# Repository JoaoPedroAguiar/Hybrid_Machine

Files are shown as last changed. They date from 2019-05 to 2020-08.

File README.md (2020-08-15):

# Hybrid_Machine
Development of a Hybrid Rapid Prototyping System Using 3D Printing Software and Arduino

Attention: This documentation is under construction.

Here, you can find all documents to replicate the project.
This machine was made to attain the title of electrical engineer, and with these documents is possible to make prototypes 
using hybrid manufacture, to save money no lost quality, and using fewer manufacturing materials. We have made it combining 
the best qualities of technology additive and subtractive.
I'm so sorry but the paper was written in the Portuguese language, probably I will write a new version in English still in 2020.

Thanks for reading and share your projects too.

Made in Brazil.

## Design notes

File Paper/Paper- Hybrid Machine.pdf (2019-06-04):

Resumo—Prototipagem rápida é um tecnologia imprescindível por possibilitar o desenvolvimento de novos produtos, e trazer uma economia de, pelos menos, 70% a 90% nos quesitos tempo e custo. Cada vez mais usadas, em consequência do barateamento das máquinas nos últimos anos. A manufatura híbrida surge com a tarefa de otimizar os processos de produção, combinando o que existe de melhor no método aditivo e subtrativo, para reduzir o volume de material, sem perder em acabamento e qualidade. A relevância da pesquisa está em apresentar uma máquina robusta e de fácil manuseio, que utiliza um sistema eletrônico de baixo custo e código fonte aberto. Que necessita de apenas um software de controle, para executar processos de manufatura híbrida, sendo uma opção aos métodos propostos anteriormente. Portanto, o objetivo da pesquisa é descrever os requisitos necessários para que se possa replicar o projeto, identificar melhorias, ilustrar os pontos fracos e apresentar os resultados. Construir um mancal, foi um sucesso, pois, permitiu demostrar de forma satisfatória, a eficiência do método. Capaz de construir peças complexas, com precisão e agilidade, em uma única estrutura mecânica.

Palavras Chave—manufatura aditiva, comando numérico computadorizado (CNC), manufatura híbrida, manufatura subtrativa, impressão 3D.

I. INTRODUÇÃO
prototipagem rápida é uma tecnologia que surgiu no final da década de 80. Com isso, foi possível construir peças a partir de um modelo tridimensional feito em programas CAD (Computer Aided Design – Desenho Assistido por Computador) [1]. Imprescindível por possibilitar o desenvolvimento de novos produtos em menor tempo e permitir verificar funcionalidades como forma, cor, tempo de manufatura e encaixes das peças [2]. Possibilitando, assim, uma maior interação com o projeto antes de ser produzido em escala, evitando retrabalhos e produtos lançados no mercado com falhas. E mais: a prototipagem pode trazer uma economia de, pelo menos, 70% a 90% nos quesitos tempo e custo [3] [4]. Duas variáveis importantíssimas para as indústrias que precisam manter a sua competividade no mercado e, ao mesmo tempo, necessitam entregar um produto de alta qualidade e acabamento impecável [5].
Com isso, sistemas híbridos de prototipagem rápida, que combinam tecnologias de deposição e remoção de material, estão sendo utilizados para otimizar a produção, integrando as características positivas de cada método [6]. A produção se torna mais eficiente quando se reduz o volume de material ao aplicar a manufatura aditiva. Esse método possui acabamento com pouca resolução. Logo, para contornar essa variável, utiliza-se, em conjunto, o processo de manufatura subtrativa, que é caracterizada por usinar as peças, remover rebarbas e eliminar deformações [7].
Para tanto, já existem máquinas híbridas contendo inúmeras ferramentas integradas a uma única estrutura mecânica, que combinam o processo de manufatura aditiva e subtrativa para criar peças otimizadas, como a de produção comercial Integrex i-400 AM [5]. Porém, a utilização desta técnica ainda é baixa, por se tratar de uma tecnologia recente e que tem sido embarcada em máquinas com alto custo de investimento. Logo, a comunidade científica tem publicado estudos visando democratizar a implementação do processo de manufatura híbrida. Para citar dois exemplos: a adaptação de ferramentas de fresagem em impressoras 3D [8], e até mesmo, a criação de uma máquina de 5 eixos, construída a partir do zero [9].
A relevância da pesquisa está em apresentar uma máquina robusta e de fácil manuseio, que utiliza um sistema eletrônico de baixo custo e código fonte aberto. Que necessita de apenas um software de controle [10] para executar processos de manufatura híbrida, como opção aos propostos anteriormente
[11] [9]. Portanto, o objetivo da pesquisa é descrever os requisitos necessários para que se possa replicar o projeto, identificar melhorias, ilustrar os pontos fracos e apresentar os resultados. Com a efetiva contribuição para a sociedade e meio ambiente, ao otimizar tempo e custo de produção, aproveitar melhor os recursos naturais e possibilitar uma gama maior de aplicações em apenas uma máquina. Sendo capaz de construir peças de alta complexidade, precisão e agilidade, mantendo os usuários competitivos frente aos desafios do mercado.
Por fim, vale ressaltar que esta é uma pesquisa open source, que visa apenas o compartilhamento de conhecimento com a comunidade científica, indexada publicamente na plataforma de hospedagem GitHub. Lá é possível encontrar toda documentação gerada durante a execução do trabalho como, vídeos, esquemáticos, firmware, modelos tridimensionais, fotos, parâmetros de configuração, manuais e artigos de referência [12].

# Desenvolvimento de um Sistema Híbrido de Prototipagem Rápida Utilizando Software de Impressão 3D e Arduino

Santos, P. A. Joao; Macedo, P. L. Pedro; Delmondes Rômulo; Araújo A. A. Marcelo

A

II. TÉCNICAS DE MANUFATURA
A manufatura é empregada em diversos campos, como medicina, educação, decoração, engenharia etc. Existem diversas técnicas e dentre as mais utilizadas podemos destacar duas delas: a aditiva, que consiste na impressão do objeto a partir do zero; e a subtrativa, cujo processo é realizado a partir da remoção do material. Contudo, estes dois métodos apresentam limitações e, se mal utilizados, podem gerar custos excedentes de produção. Nos últimos anos, a manufatura híbrida, método que combina a tecnologia aditiva e subtrativa, tem sido utilizada por reduzir custo e tempo de produção, se comparado com os métodos realizados separadamente [11].
A. Manufatura Aditiva
Esse processo é feito em camadas, que se sobrepõe uma a outra, como uma espécie de soldagem do material escolhido. Previamente, é realizado um desenho tridimensional em CAD do objeto. Para somente depois imprimir seu resultado. Hoje, a impressão 3D utiliza inúmeros materiais, como polímeros, pó, cerâmica, metal, compostos alimentícios, gel, concreto, dentre outros [13].
Logo, a tecnologia de manufatura aditiva é escolhida por usuários que visam construir peças de forma rápida e com alta complexidade, mas que não se preocupam tanto com o acabamento das mesmas [2]. Alguns exemplos bastantes conhecidos desse método: LENS (Laser Engineered Net Shaping – Modelagem por Laser de Engenharia), SLA (Stereolithography - Estereolitografia), SLS (Selective Laser Sintering – Sintetização por Laser Seletivo) e SDM (Shape Deposition Manufacturing) [14]. Apesar da manufatura aditiva apresentar detalhes de qualidade na impressão, sua popularidade aumenta a cada ano, tanto no meio acadêmico, como no comercial e pessoal. Acredita-se que o uso dessa tecnologia será bem frequente e comum, sendo possível confeccionar componentes elétricos e eletrônicos, como um smartphone [15].
B. Manufatura Subtrativa
A máquina de fresagem CNC é o melhor exemplo de máquina de manufatura subtrativa, cuja função principal é controlar os movimentos da ferramenta e peça de trabalho. Ela permite, sempre que necessário, a troca da fresa, broca e outras ferramentas [16]. Alguns métodos são mais utilizados para fazer a extração do material, dando, assim, a forma desejada, como fresamento, perfuração e torneamento.

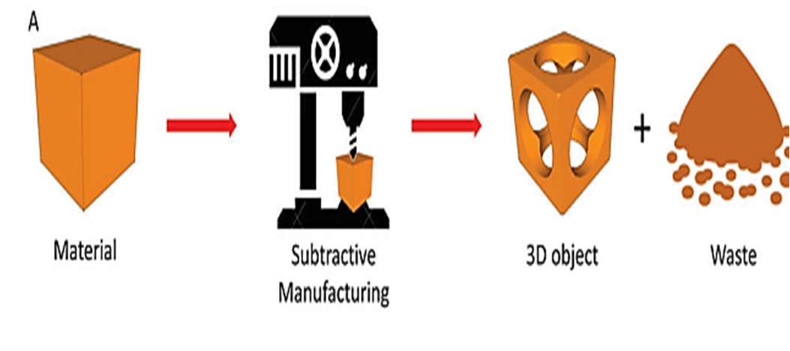
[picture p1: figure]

Fig. 1. Processos da tecnologia de manufatura subtrativa

Assim, sabe-se que a alta resistência das peças, ocorre devido sua única camada de matéria prima, fazendo com que o resto do desbaste não seja utilizado, Fig. 1 [17]. Algumas geometrias são incapazes de serem confeccionadas e a longa duração necessária para sua produção é uma das características negativas deste método [17].
C. Manufatura Híbrida
A manufatura híbrida une as melhores características de cada modelo citado, ao executar geometrias complexas, diminuir o tempo de produção e aproveitar melhor a matéria prima. Conforme a Fig. 2 [5], a primeira etapa consiste em adicionar material em camadas para construir um sólido de baixa resolução no menor intervalo de tempo e, em seguida, utilizar a tecnologia de manufatura subtrativa para cortar as rebarbas e melhorar o acabamento [9].
Características individuais presentes em cada processo podem ser encontradas em uma só máquina, que começa a surgir no mercado como a Integrex i-400 AM, modelo industrial que integra diversas tecnologias de manufatura [5].

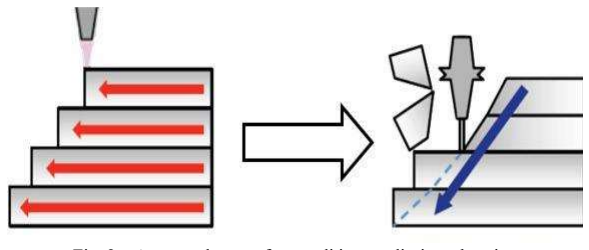
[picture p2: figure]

Fig. 2. A esquerda manufatura aditiva e a direito subtrativa.

III. FERRAMENTAS DE MANUFATURA
No mundo contemporâneo cria-se a necessidade de substituir as ferramentas pelas máquinas, a produção artesanal pela industrial e a energia humana pela energia eletromecânica. Dentro desse contexto, surge então a fresadora com comando numérico computadorizado (CNC). Marco relevante na história da indústria, por unir flexibilidade e versatilidade com precisão e um bom acabamento superficial. Diferente dos meios artesanais, que demandavam bastante tempo e não apresentavam a mesma qualidade [18].
Existem vários parâmetros que podem ser alterados no processo de manufatura. Alguns exemplos: determinação de ferramentas de trabalho, profundidade de corte, velocidade de avanço e velocidade de corte. As metodologias de remoção de material mais conhecidas são o torneamento, a fresagem, o aplainamento, a furação e a serragem [19].
Uma infinidade de materiais de manufatura pode existir quando se trata de produção aditiva e subtrativa. E podem ainda abranger diversas áreas, desde a confeitaria à corrida aeroespacial. Tratando-se de manufatura subtrativa, boa parte dos elementos conhecidos ou confeccionados pelo homem estão aptos para este método. Já na aditiva se destacam alguns, em específico, na forma de polímeros, como o PLA (Poly Lactic Acid - Poliácido Láctico) e o ABS (Acrylonitrile Butadiene Stryrene – Copolímero de Acrilonitrila) [2].

A. Ferramentas de Corte
A remoção do cavaco da peça é feita por usinagem, por meio de uma ferramenta de corte. A alta qualidade do processo está atrelada à eficiência desta ferramenta. Já o tempo de vida útil é diretamente proporcional ao tempo de corte efetivo das suas arestas de trabalho - antes de amolar ou fazer a troca da ferramenta [19].
O modelo mais comum de ferramenta de corte é a fresa. Bastante versátil, o instrumento é capaz de executar várias operações, como confeccionar roscas, abrir ranhuras e superfícies planas, e ainda fazer o processamento de engrenagens, dentre outras habilidades. Seus principais parâmetros: velocidade de corte, velocidade de avanço, penetração, taxa de remoção do material e tempo de produção. Existem quatro modelos diferentes de fresadoras; as verticais, as horizontais, as especiais e a universal. Elas podem ser utilizadas de duas maneiras – desde que sempre rotacione a ferramenta. Na fresagem cilíndrica, o eixo é paralelo à superfície; e na fresagem de topo (ou frontal), está perpendicular à área de trabalho. Conforme a Fig. 3 [18].

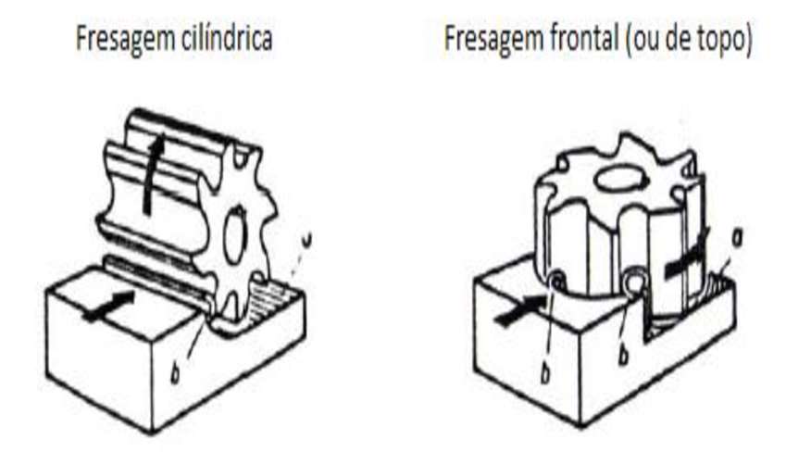
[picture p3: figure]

Fig. 3. Métodos de fresagem

B. Materiais de Impressão
Diversos materiais podem ser utilizados para a confecção de objetos 3D, incluindo metais, cerâmicas, polímeros, compostos alimentícios e sistemas biológicos [13]. São, basicamente, três estágios de manipulação: líquido, pó ou sólido base [7]. Em tese, os polímeros são os mais utilizados atualmente para impressão. Exemplos: PLA, ABS, policarbonatos, nylon e PETG (Polyethylene Terephthalate Glycol – Polietileno Tereftalato Glicol). Existem também materiais que, caso exposto a raios gama ou à óxido de etileno, se solidificam, comumente usados em tecnologias médicas [16].
O PLA é o filamento mais utilizado por não ser tóxico, ser biodegradável e possuir baixa temperatura para ponto de fusão, tornando-o mais ecologicamente sustentável [20]. Mesmo apresentando características mecânicas superiores e custo reduzido, o ABS não é tão usual quanto os demais. Isso devido à liberação de gases tóxicos e à maior exigência de temperatura de trabalho da extrusora, assim como da mesa aquecida. O PETG é considerado como o meio termo entre ABS e PLA, sendo mais durável e flexível que o PLA, e ainda mais fácil de imprimir que o ABS [21].

IV. MATERIAIS E MÉTODOS
Pesquisa exploratória e experimental, iniciada como tema de Trabalho de Conclusão de Curso, em 2016 [22], com foco na construção de uma máquina capaz de confeccionar placas de circuito impresso, de estrutura robusta e intercambiável. Conforme Fig. 4 [22]. Em 2017, novos objetivos foram traçados, a fim de tornar a movimentação da máquina intercambiável entre impressora 3D e fresadora CNC. Nessa, nova fase, damos continuidade ao trabalho, para que sejam feitas modificações na estrutura mecânica, elétrica e eletrônica. Objetivo: torná-la híbrida, de fácil manuseio e com troca rápida de ferramentas de fixação. Para isso, mantemos a proposta inicial de ser uma máquina modular, robusta e de fácil manuseio.

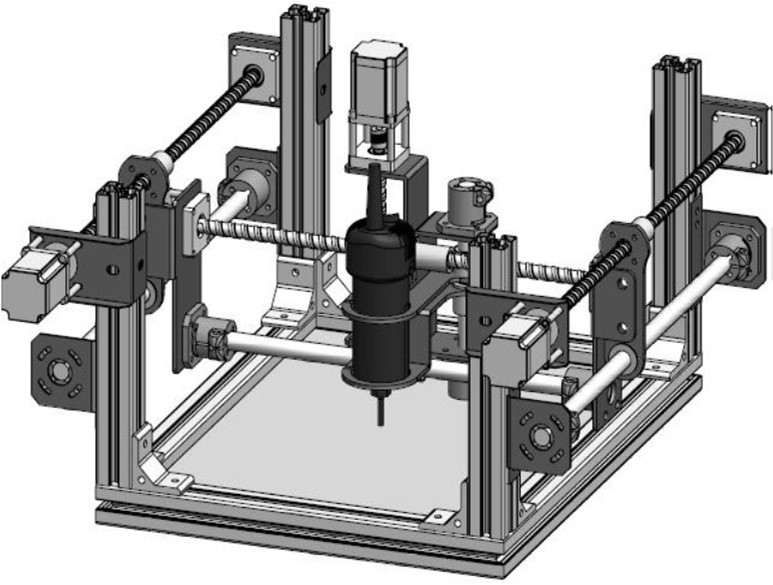
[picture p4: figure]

Fig. 4. Máquina intercámbiavel

A eletrônica da máquina é composta pelo sistema embarcado Arduino Mega, conectada ao módulo complementar de acionamento, Ramps 1.4. O Arduino é carregado com o firmware Marlin, que possui rotinas e estruturas lógicas adequadas ao projeto, todos de código fonte aberto, com atualizações constantes. Máquinas industriais empregam apenas um software de controle com funções nativas, para executar processos de manufatura híbrida. Porém, esses programas possuem rotinas de criptografia que bloqueiam a utilização em máquinas que não sejam produzidas por esses fabricantes. Até o presente momento, a pesquisa não identificou um software aberto aos usuários, com funções nativas de manufatura híbrida. Entretanto, alguns estudos têm apresentado alternativas que possibilitam a utilização desta técnica.
A primeira delas [11] consiste em utilizar dois softwares de controle distintos, para executar a manufatura aditiva e subtrativa, em ambientes de controle e supervisão separados. Pois, são encontrados inúmeros softwares abertos e dedicados à tecnologia, com suporte para serem empregados em conjunto com o sistema embarcado Arduino Mega. Em outro estudo [7], utiliza-se um software aberto e comercial, em conjunto com um programa desenvolvido pelos pesquisadores, que permite movimentar as ferramentas em uma máquina de cinco eixos. Como alternativa, apresentamos uma metodologia que utiliza apenas o software aberto de impressão, Simplifly3D, que depende apenas de algumas modificações não usuais, para construir uma peça efetivamente híbrida [12].

V. RESULTADOS
A primeira tarefa foi reinstalar [22] a tupia elétrica de 530 watts - com velocidade regulada de 0 a 30 mil rotações por minuto - à estrutura mecânica. Conforme a Fig. 5. Ela é responsável por rotacionar uma fresa instalada em seu eixo, tornando possível fresar na vertical sólidos de diversos materiais, como alumínio, madeira e plástico.

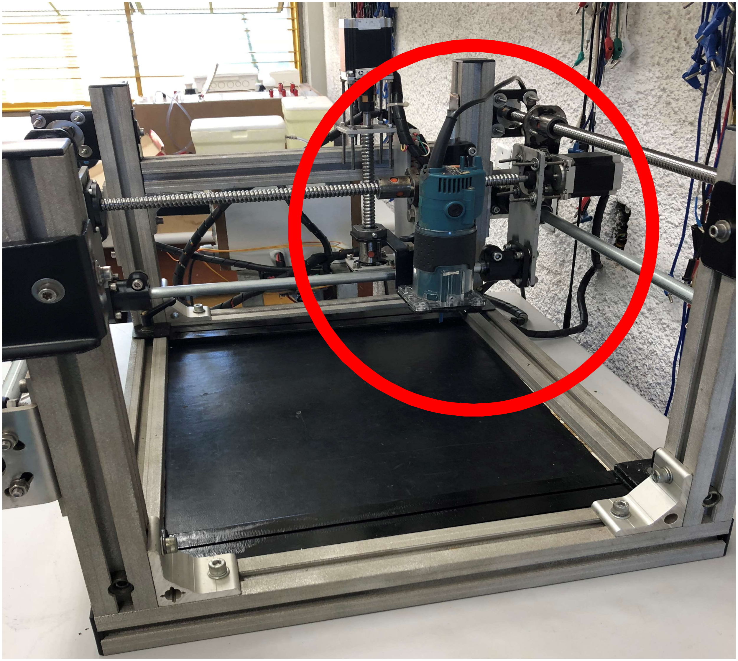
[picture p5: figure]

Fig. 5. Tupia fixada na máquina

A regulagem de altura é feita de forma manual, rápida e sem a utilização de ferramentas. Assim, após a instalação da tupia, que possuiu cerca de 1500 gramas, testes foram realizados para corrigir os parâmetros de movimentação decorrente do peso acrescentado à estrutura mecânica. A Tabela 1 apresenta as novas velocidades de trabalho da máquina, reconfiguradas no firmware Marlin.

TABELA I. DADOS DE VELOCIDADE

Parâmetros Configurados no Software Simplify3D
Retraction Speed (mm/min) | Default Printing Speed (mm/min) | X/Y Axis Movement Speed (mm/min) | Z Axis Movement Speed (mm/min) | X/Y Probe Speed (mm/min)
402.0 | 600.0 | 600.0 | 600.0 | 300.0

Para validar a utilização da máquina em processos de manufatura subtrativa foi elaborado um modelo tridimensional no software de modelagem Blender. Esse modelo possuiu espessura uniforme de 3 mm, carregado no Simplify3D, conforme a Fig. 6, para ser manufaturado em três materiais: MDF (Medium-Density Fiberboard), acrílico e placa de fenolite. Como as peças que seriam fresadas tem no máximo 3mm de profundidade, é imprescindível o uso da função de auto nivelamento. Ela compensa em software os desníveis da superfície, mapeando diversos pontos dá área de trabalho [23] [10]. Com o término do processo, os dados são gravados na memória não volátil do microcontrolador Atmega 2560, presente no Arduino Mega. Isso possibilita a leitura dos dados mesmo após desenergizar o sistema. Dessa forma, o processo é executado apenas quando a estrutura é movimentada.

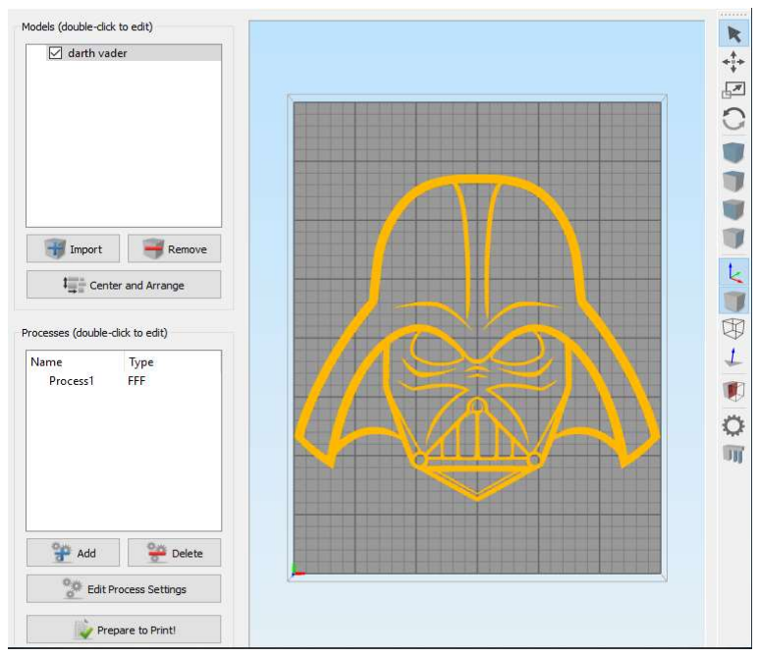
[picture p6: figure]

Fig. 6. Modelo tridimensional

Após o nivelamento, algumas funções foram habilitadas e configuradas, para permitir que o software execute processos de manufatura subtrativa, tendo em vista que ele não possuiu funções e suporte nativo para este tipo de aplicação, conforme os parâmetros presentes no folder (Router CNC Configuration), hospedado no GitHub [12]. Possibilitando, assim, o início dos testes de validação da tecnologia de manufatura subtrativa, o primeiro material utilizado foi o MDF, por apresentar características mecânicas favoráveis de fresagem. Na Fig. 7 é apresentado o resultado do processo que utilizou uma fresa reta de 6mm de diâmetro acoplada à tupia e metade da velocidade nominal, o modelo foi fatiado em três camadas de 1mm, para que a ferramenta penetrasse o MDF gradualmente.

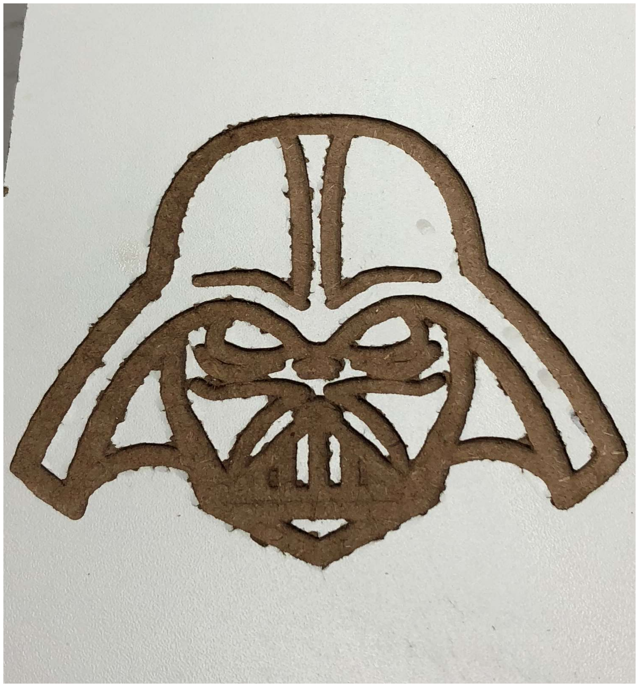
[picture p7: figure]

Fig. 7. Manufatura subtrativa em MDF

Outros dois materiais foram selecionados para serem fresados conforme a Fig. 8, o acrílico na parte superior, com configurações idênticas ao utilizado no MDF, e na parte inferior da Fig. 8, uma placa de fenolite com penetração unitária de 1 mm, fresa reta de 3.2 mm de diâmetro e velocidade nominal da tupia. Ao término, foi iniciado a implementação da tecnologia de manufatura aditiva à máquina. Para tal, foi necessário introduzir novos componentes elétricos e eletrônicos ao sistema, como mesa aquecida, extrusora, sensores de temperatura, relé de estado sólido e troca dos conectores do módulo Ramps por um modelo que possui proteção contra inversão de polaridade e maior resistência mecânica.

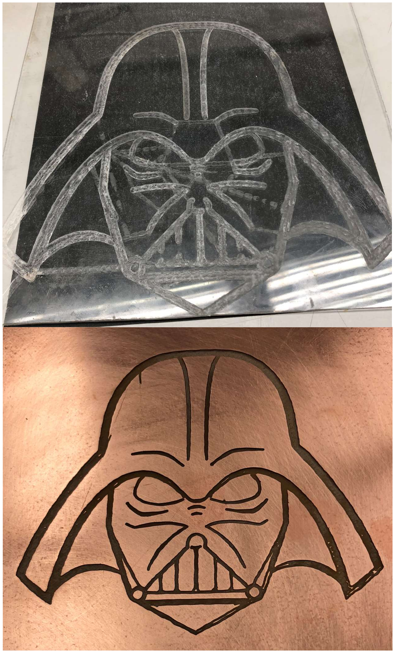
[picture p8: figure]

Fig. 8. Manufatura subtrativa em acrílico e placa de fenolite

Portanto, visto que a extrusora não possuiu o mesmo formato que a tupia, um suporte mecânico foi construído para que ela possa ser inserida no mesmo local. Conforme a Fig. 9. Esse suporte possui dois componentes móveis, para ajustar a posição do bico da extrusora em relação à superfície de impressão. Para executar uma troca rápida entre tupia e extrusora, foram utilizados quatro ímãs de neodímio com 10 mm de diâmetro por

### 4 mm de espessura, que atraem o suporte da extrusora à

estrutura mecânica do eixo Z, excluindo o uso de ferramentas para fixação. Conforme a Fig. 9. A troca é feita aplicando um esforço com as mãos no sentido contrário ao campo magnético do ímã.

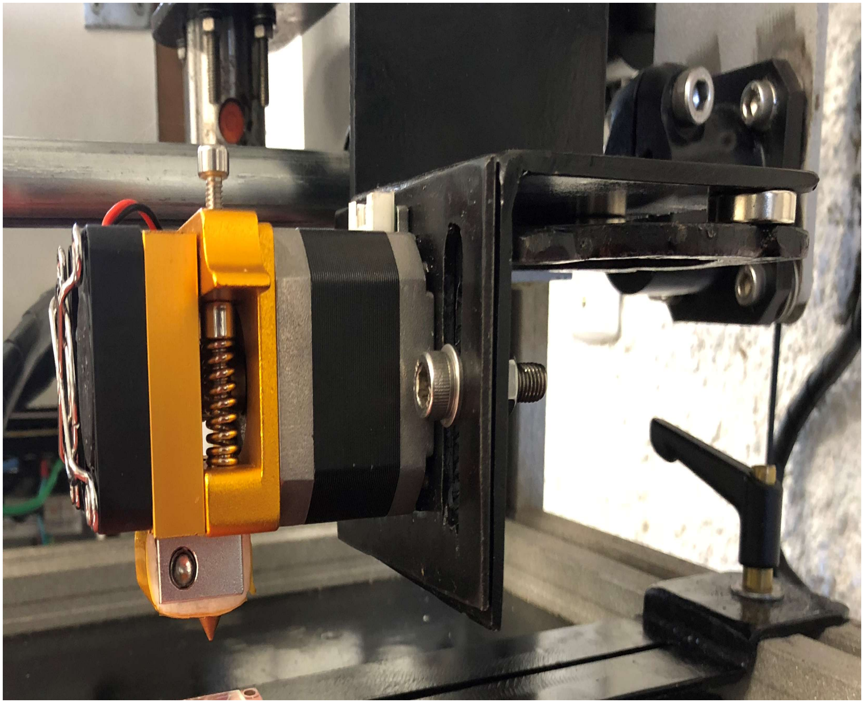
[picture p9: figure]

Fig. 9. Suporte de fixação da extrusora com ímãs de neodímio

Em seguida, duas guias metálicas ajustáveis foram inseridas para fixar a mesa aquecida. De acordo com a Fig. 10. A principal função das guias é descartar a necessidade de furar qualquer ponto da estrutura, caso seja necessário modificar a posição da mesa. Para iniciar o processo de impressão, foi selecionado o material ABS, que precisa ser aquecido pela extrusora, em temperaturas que vão de 230ºC à 240ºC.

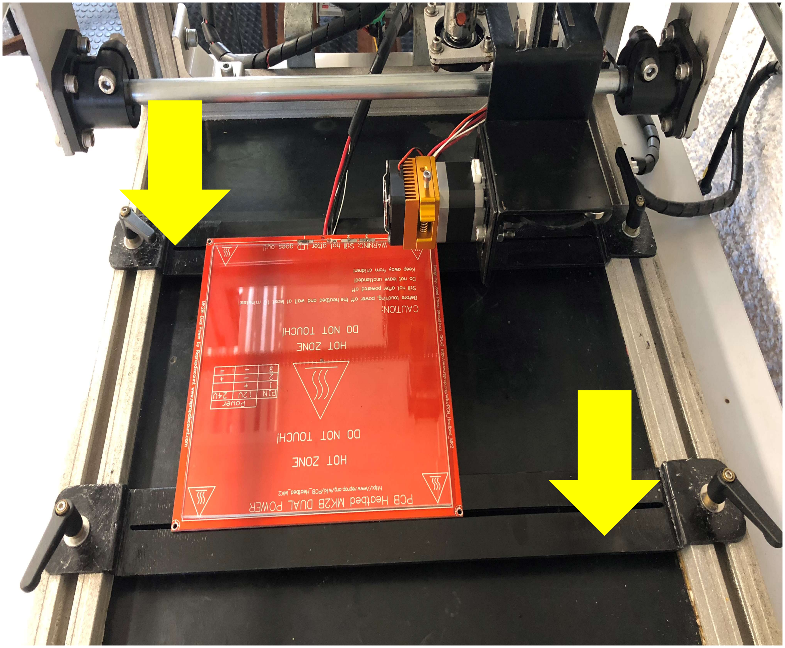
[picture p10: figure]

Fig. 10. Suporte da mesa aquecida

Entretanto, foi necessário controlar a temperatura da extrusora por um controlador proporcional integral derivativo (PID), obtendo maior estabilidade e precisão do sistema. Conforme o controle de malha fechada apresentada na Fig. 11. Desta maneira, a temperatura da extrusora é controlada, variando a tensão média sobre os terminais da resistência de aquecimento por PWM (Pulse Width Modulation – Modulação por Largura de Pulso). Pois a temperatura da resistência varia em função da tensão aplicada.

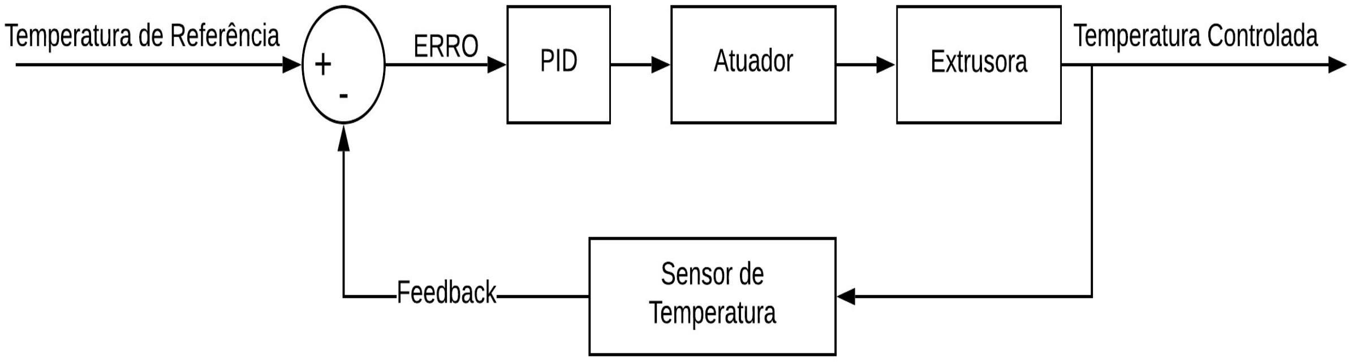
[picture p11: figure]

Fig. 11. Controle de Macha Fechada

Para facilitar a implementação do PID, o firmware Marlin apresenta uma rotina no código chamada de PID Autotune, que utilizada o método de ajuste Ziegler-Nichols [24]. Esse é um método heurístico que define os termos dos controladores proporcional, integral e derivativo - automaticamente. Apresentamos, na Tabela 2, os valores medidos experimentalmente, que definem o desempenho do controlador, em função da quantidade de ciclos de otimização.

TABELA II. DESEMPENHO DO CONTROLADOR PID

Parâmetros Medidos em Laboratório
Ciclos | 8 | 10 | 20
Controlador Proporcional (KP) | 16,87 | 15,75 | 15,95
Controlador Integral (KI) | 1,2 | 1,06 | 1,09
Controlador Derivativo (KD) | 59,43 | 58,51 | 58,14
Set Point (°c) | 230 | 230 | 230
Temperatura Inicial (°c) | 25 | 26 | 26,5
Tempo de Assentamento (s) | 101 | 132 | 139
Tempo de Pico (s) | 101 | 115 | 104
Ultrapassagem Percentual (%) | 0,87 | 0,3 | 0,41
Erro Permanente (°c) | 4 | 1,56 | 1,81

Para imprimir com ABS, a mesa também precisa ser aquecida com uma temperatura de aproximadamente 100°C, para auxiliar a aderência do filamento sobre a superfície.

Porém, não foi necessário realizar o controle PID, pois a temperatura máxima alcançada ficou próximo de 100°C. Assim, a mesa só é acionada antes de iniciar a impressão. E desligada após o término, pelo relé de estado sólido. Concluindo, neste momento, todas as modificações pertinentes. Resultado que pode ser visto no diagrama de blocos da Fig. 12.

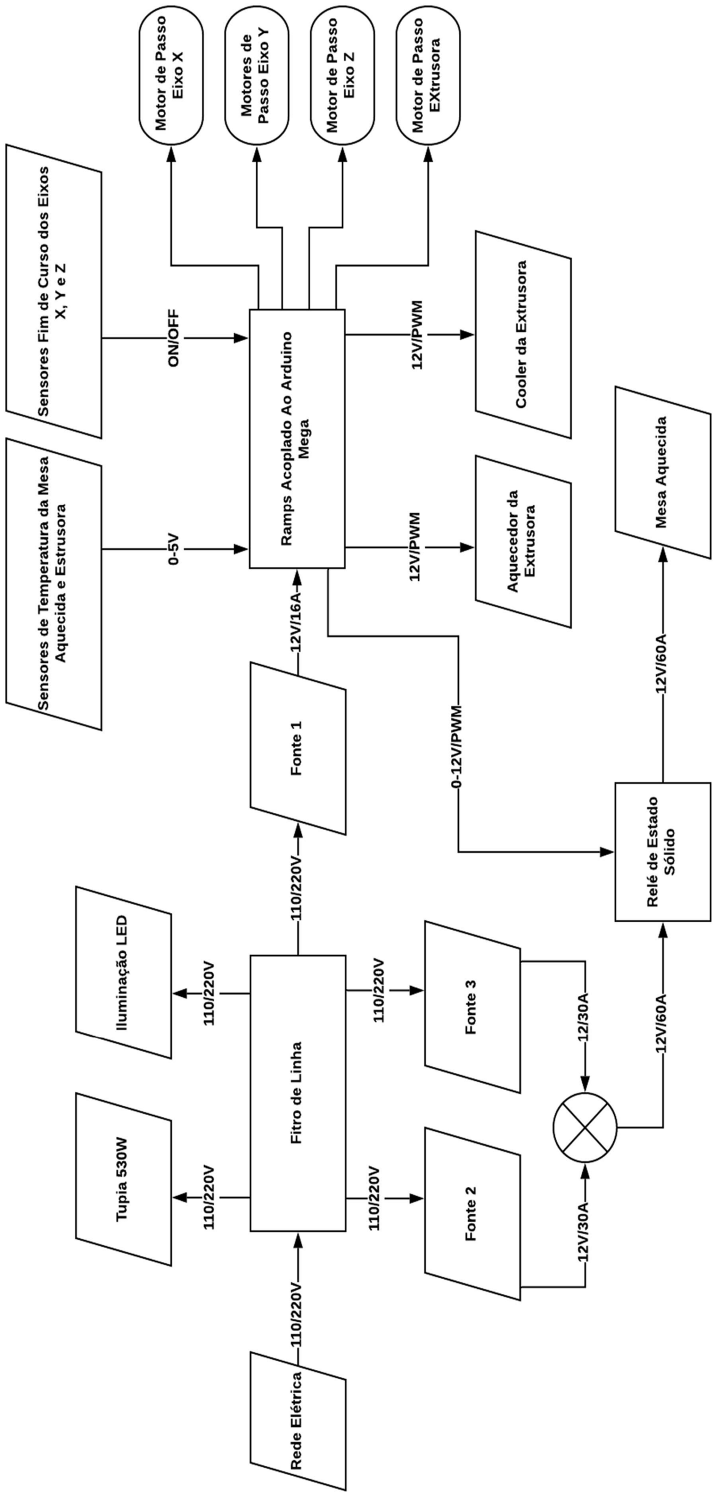
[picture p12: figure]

Fig. 12. Diagrama de Blocos da Máquina

Para encontrar os parâmetros de funcionamento da função de impressão 3D, algumas peças foram impressas em pequena escala para avaliar quais valores poderiam ser otimizados. Conforme Tabela 3. Pois, como o modelo mecânico da máquina é único, não foi possível usar dados de outra máquina como referência. Vale ressaltar, ainda, que todas as peças impressas foram feitas utilizando ABS de 1.75mm e bico extrusor de 0.6mm de diâmetro.

TABELA 3. CONFIGURAÇÃO UTILIZADA NO PROCESSO DE IMPRESSÃO

Parâmetros Configurados no Software Simplify3D
Retraction Speed (mm/min) | Default Printing Speed (mm/min) | X/Y Axis Movement Speed (mm/min) | Z Axis Movement Speed (mm/min) | Infill Percentage (%)
350 | 450 | 450 | 250 | 50

O sólido selecionado para ser impresso foi um mancal. Por fazer parte dos requisitos necessários para melhorar a estabilidade da máquina. Está peça demorou aproximadamente onze horas e doze minutos para ser impressa e gastou 48 gramas de filamento - em um total de 15,6 metros. Conforme Fig. 13. Logo após, a extrusora é substituída pela tupia, para que a peça seja fresada e acabada, até chegar ao estado final projetado. Esse modelo foi concebido para ser confeccionado utilizando a tecnologia de manufatura híbrida.

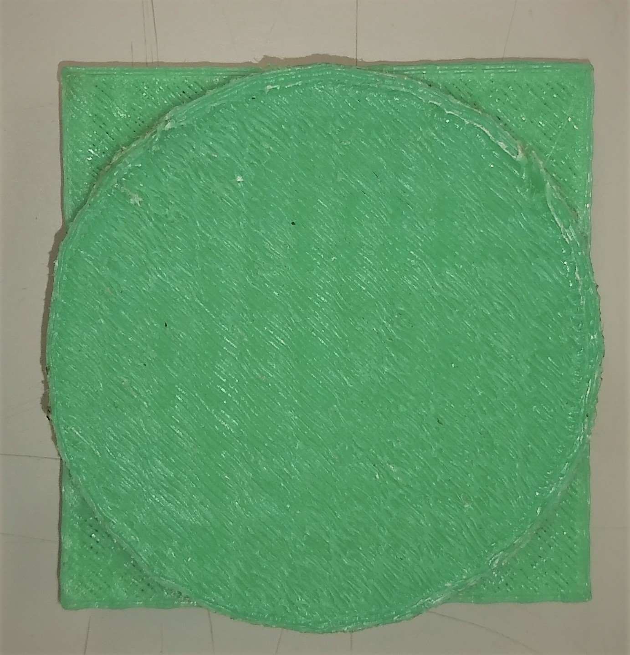
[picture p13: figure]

Fig. 13. Mancal Impresso

Com isso, uma ferramenta de corte de 3.2 mm de diâmetro é fixada junto à tupia, para fresar quatro furos nas extremidades. Conforme Fig. 14. O processo levou cerca de dois minutos para ser concluído, utilizando os parâmetros de velocidade apresentados na Tabela 1. Esses furos, vale frisar, não foram feitos inicialmente, porque a técnica subtrativa apresenta características mais favoráveis, como precisão e acabamento

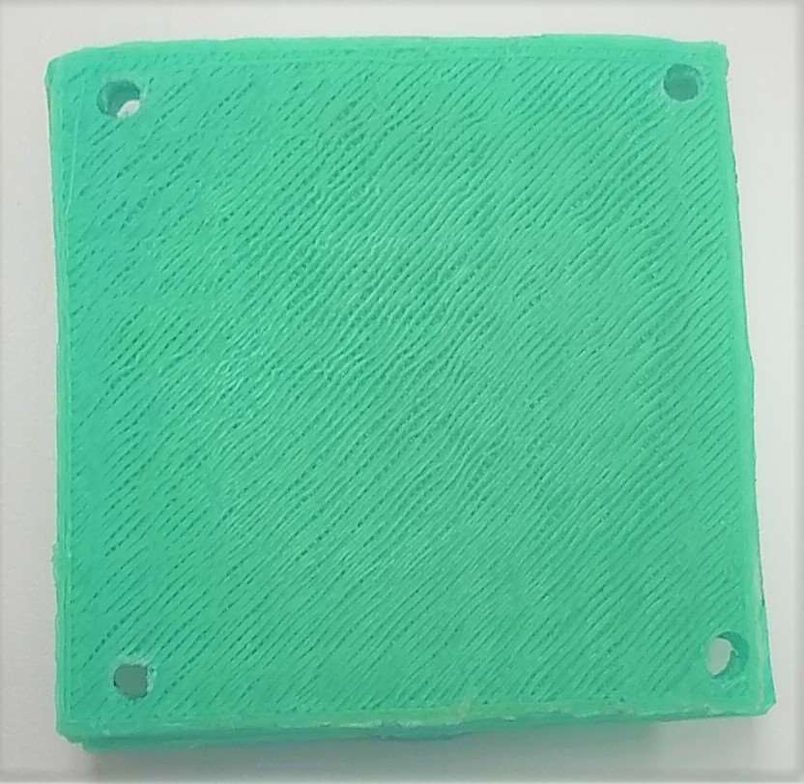
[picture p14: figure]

Fig. 14. Primeira Parte do Fresamento

Por fim, é dado continuidade ao processo, fresando a parte interna da peça, com a tupia em velocidade nominal – evitando assim o travamento do eixo de rotação. Esse processo demorou apenas seis minutos para ser finalizado, apresentando um bom acabamento interno. Conforme Fig. 15. Portando, esta peça apresenta o resultado, do sistema híbrido de prototipagem rápida utilizando software de impressão 3D e Arduino.

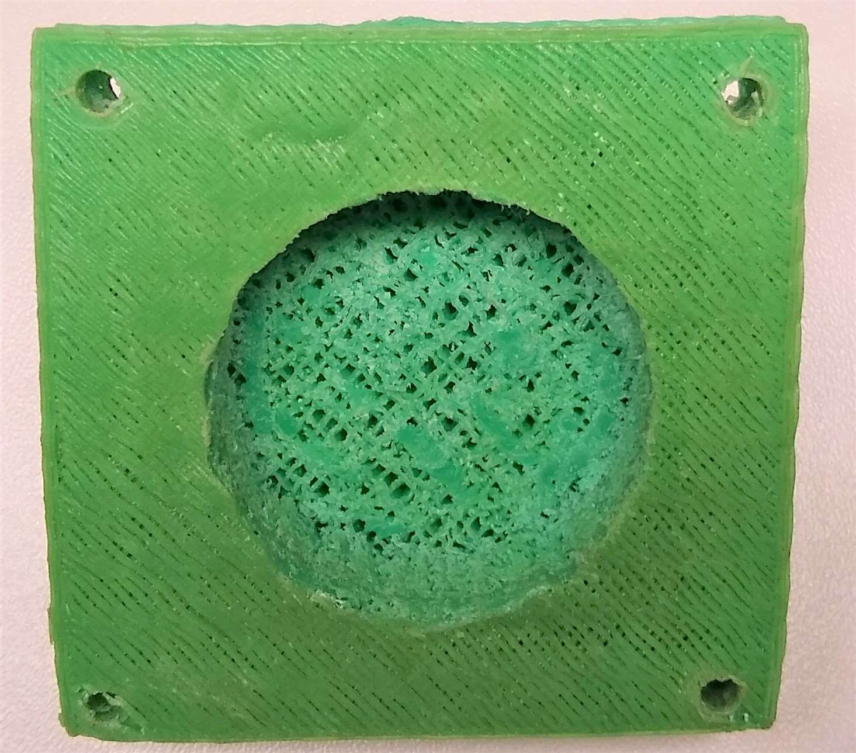
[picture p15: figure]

Fig. 15. Acabamento Final

O resultado da máquina, com todos os periféricos devidamente instalados e configurados, pode ser visto na Fig.

### 16. Um acervo com a documentação completa da máquina, está

indexado publicamente na plataforma online GitHub [12].

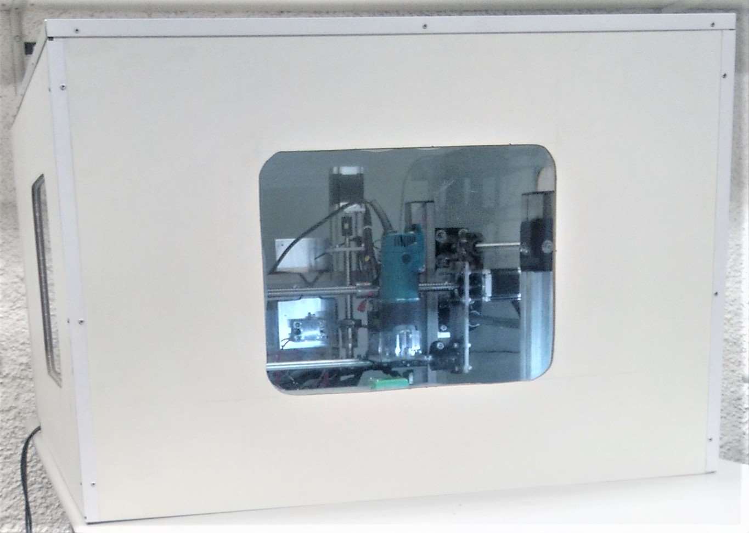
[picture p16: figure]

Fig. 16. Máquina Híbrida Utilizada

VI. DISCUSSÕES
A instalação da tupia à estrutura resultou no aumento do esforço realizado pelos motores para movimentar a mesa. Contudo, a intensidade de corrente fornecida foi elevada para aumentar a faixa de torque, juntamente com a diminuição da velocidade dos eixos. Isso permitiu que a máquina conseguisse, além de movimentar o peso excedente, realizasse esforços ao fresar materiais mais duros como o acrílico. Porém, o acionamento e o controle de velocidade da tupia ainda são feitos de forma manual. Assim, caso o processo de manufatura termine, o usuário precisa desligar a tupia manualmente.
Vale ressaltar: para tornar o processo mais eficiente é necessário utilizar de forma consciente as ferramentas de trabalho, selecionando sempre a mais adequada para cada material [24]. As fresas utilizadas foram todas selecionadas de acordo com o material fresado, evitando esforços excedentes pela máquina realizar o corte. Testes utilizando materiais mais duros, como ligas metálicas, por exemplo, podem requisitar mais torque dos motores. Contudo, os ensaios desses materiais não foram executados porque a extrusora não é capaz de utilizar materiais metálicos.
O software Simplify3D foi capaz de suportar a utilização da tupia mesmo sem suporte para este tipo de ferramenta. Entretanto, o fatiamento do modelo tridimensional - que define como a ferramenta irá se movimentar - é dedicado aos processos de manufatura aditiva. Com isso, o caminho pelo qual a fresa irá percorrer pode não ser o mais otimizado para este tipo de aplicação. A utilização do suporte com ímãs nas extremidades permitiu que a troca de ferramentas seja feita de forma rápida e descomplicada. O método, comparado com máquinas industriais que possuem sistemas automatizados de troca, possibilitou a redução de custo de fabricação e a maior facilidade de implementação.
Quanto à impressão 3D, inicialmente, a mesa aquecida não estava alimentada pela tensão da fonte de 12 volts, sendo apenas ligada e desligada pelo relé de estado sólido. A ideia era aplicar a tensão da rede de 220V sobre a mesa, variando o valor médio da tensão por PWM, utilizando o controlador PID. A principal vantagem estaria em alcançar os valores de setpoint, de forma mais rápida. Porém, a resistência de 0,3 Ohm é muito baixa para este tipo de aplicação. Pois, caso o sistema embarcado trave, a mesa pode exigir uma corrente de aproximadamente 733 amperes, causando o acionamento do sistema de proteção contra curto circuito da instalação elétrica.
Já na parte de extrusão, as peças começaram a empenar as bordas curvando se para cima, descolando as primeiras camadas, esse problema impossibilitava o término do processo. Pois, devido ao aumento de altura da peça, o bico da extrusora acabava empurrando a peça para outra posição, inutilizando o protótipo. Em um dos casos o problema foi tão sério, que o vidro que fica em cima da mesa aquecida acabou quebrando, junto aos acoplamentos dos motores. Pois, a peça conseguiu bloquear um dos eixos da máquina. Para contornar este problema, um gabinete foi construído. Conforme Fig. 16. Com o intuito de manter a temperatura interna constante, pois o ABS é um termoplástico que sofre contração, caso a peça seja exposta à variação de temperatura.
Outro ponto que merece bastante atenção, está relacionado com os problemas de EMC (Electromagnetic Compatibility – Compatibilidade Eletromagnética) que impedem que a máquina complete qualquer trabalho de impressão. O primeiro, causado por EMI (Eletromagnetic Interference – Interferência Eletromagnética), reiniciava o microcontrolador, devido à proximidade do Arduino Mega, em relação aos cabos pelo qual fluía toda corrente alternada, drenada pelas fontes chaveadas. O problema foi resolvido apenas aumentando a distância do cabo, em relação ao Arduino. No segundo caso, o microcontrolador travava, sem que qualquer mensagem de erro fosse retornada, voltando ao normal só após resetar o microcontrolador. Resolvido, trocando o cabo de comunicação - do Arduino com o computador - por um modelo com blindagem eletrostática e filtro de supressão de ruídos de alta frequência, conhecido como Ferrite Bead.

VII. CONSIDERAÇÕES FINAIS
A utilização do conjunto de baixo custo e open source, Arduino Mega, módulo Ramps 1.4 e firmware Marlin, combinados com o software aberto de controle e supervisão, Simplifly3D. Foi um sucesso por permitir que processos de manufatura híbrida, fossem realizados facilmente a partir de um único software. Embarcados em uma estrutura mecânica robusta e de fácil manuseio, viabilizado pela utilização de ímãs e conectores de engate rápido com proteção contra inversão de polaridade, tornando a troca de periféricos mais rápida e segura. Fresar a placa de fenolite, permitiu identificar que ainda é possível produzir placas de circuito impresso. Conforme visto na parte inferior da Fig. 8. Apenas modificando alguns parâmetros de movimentação, preservando a concepção inicial da máquina [22]. A construção do mancal permitiu demonstrar de forma satisfatória a proposta do estudo. Porém, acreditasse que o processo poderia ter sido otimizado imprimindo a peça com os cinco furos, com o diâmetro um pouco menor do que o esperado. Logo, a ferramenta cortaria menos material, sendo usada apenas para dar acabamento, reduzindo a quantidade de matéria prima, e o tempo necessário para imprimir e fresar. Recomenda-se, que os trabalhos futuros se concentrem em: desenvolver um sistema embarcado que seja imune aos problemas de EMI encontrados, repensar o layout da estrutura mecânica, desenvolver um software com funções nativas, imprimir com metal, criar laços com empresas e institutos de pesquisa que tenham interesse em investir no projeto. Como também, produzir protótipos encomendados pela comunidade, com o intuito de financiar bolsas de pesquisa, melhorias e aquisição de equipamentos para o laboratório. E, utilizá-la como ferramenta de popularização da ciência e tecnologia, preservando as características open source do projeto.

REFERÊNCIAS
[1] J. Fogiatto, "O uso da prototipagem rápida na área médico-odontológica", Revista Tecnologia & Humanismo, no. 30, pp. 60-68, 2006.
[2] J. Nagel, "Hybrid Manufacturing System Design and Development", in 38th Design Automation Conference, Chicago, 2012, pp. 189-198.
[3] C. Ahrens and N. Volpato, Prototipagem rápida, 1st ed. São Paulo: Edgard Blücher, 2007.
[4] A. Gorni, "Introdução à prototipagem rápida e seus processos."Plástico Industrial, pp. 230-239, 2001.
[5] T. Yamazaki, "Development of A Hybrid Multi-tasking Machine Tool: Integration of Additive Manufacturing Technology with CNC Machining", in 18th CIRP Conference on Electro Physical and Chemical Machining (ISEM XVIII), Oguchi, 2016, pp. 81-86.
[6] Z. Zhu, V. Dhokia and S. T. Newman, "A novel process planning approach for hybrid manufacturing consisting of additive, subtractive and inspection processes,"2012 IEEE International Conference on Industrial Engineering and Engineering Management, Hong Kong, 2012, pp. 1617-1621.
[7] W. Lee, C. Wei and S. CHUNG, "Development of a hybrid rapid prototyping system using low-cost fused deposition modeling and five-axis machining.", Journal of Materials Processing Technology, vol. 241, no. 11, pp. 2366-2374, 2014.
[8] G. Anzalone, B. Wijnen and J. Pearce, "Multi-material additive and subtractive prosumer digital fabrication with a free and open-source convertible delta RepRap 3-D printer", Rapid Prototyping Journal, vol. 21, no. 5, pp. 506-519, 2015.
[9] A. Kale, A. Kumar, M. Kumar and M. Prakasah, "Optimization of hybrid manufacturing process parameters by using FDM in CNC machine", in IOP Conference Series: Materials Science and Engineering, Kattankulathur, 2018, p. 012088.
[10] J. Santos, "Investigação e Aperfeiçoamento de um Sistema de Impressão 3D e Fresagem Intercambiável", 4th Brazilian Technology Symposium, 2018.
[11] P. Jorge Rodriguez, I. Pavel and A. Choudhury, "Development of a 3-D Printer and CNC Milling Desktop Machine for Manufacturing Labs", in ASEE Annual Conference & Exposition, New Orleans, 2016.
[12] J. Santos and P. Macedo, "JoaoPedroAguiar/Hybrid_Machine", GitHub,
2019. | [Online]. | Available:
https://github.com/JoaoPedroAguiar/Hybrid_Machine. [Accessed: 25-May- 2019].
[13] W. Frazier, "Metal Additive Manufacturing: A Review", Journal of Materials Engineering and Performance, pp. 1917-1928, 2014.
[14] K. Karunakaran, S. Suryakumar, V. Pushpa and S. Akula, "Low cost integration of additive and subtractive processes for hybrid layered manufacturing", Robotics and Computer-Integrated Manufacturing, no. 5, pp. 490-499, 2010.
[15] D. Espalin, D. Muse, E. MacDonald and R. Wicker, "3D Printing multifunctionality: structures with electronics", The International Journal of Advanced Manufacturing Technology, pp. 963-978, 2014.
[16] M. Müller and E. Wings, "An Architecture for Hybrid Manufacturing Combining 3D Printing and CNC Machining", International Journal of Manufacturing Engineering, vol. 2016, pp. 1-12, 2016.
[17] K. Boivie, S. Dolinsek and D. Homar, "Hybrid manufacturing; integration of additive technologies for competitive production of complex tools and products", in 15th International Research/Expert Conference, Prague, 2011.
[18] D. Pereira, "Estudo comparativo da vida útil das ferramentas e acabamento superficial para diferentes ferramentas de fresagem", Master, Escola Superior de Tecnologia e Gestão Instituto Politécnico de Bragança, 2017.
[19] A. Souza, "Aplicação de multisensores no prognóstico da vida de ferramenta de corte no torneamento", Doctor, Universidade Federal de Santa Catarina, 2004.
[20] A. Ambrosi and M. Pumera, "3D-printing technologies for electrochemical applications", Chemical Society Reviews, vol. 45, no. 10, pp. 2740-2755, 2016.
[21] K. Hamad, M. Kaseem, H. Yang, F. Deri and Y. Ko, "Properties and medical applications of polylactic acid: A review", Express Polymer Letters, vol. 9, no. 5, pp. 435-455, 2015.
[22] R. Delmondes and L. Rodrigues, "Cnc intercambiável aplicada a confecção de placas de circuito impresso.", Graduate, Pontifícia Universidade Católica de Goiás, 2016.
[23] D. Knop, "Aspectos técnicos e contribuições na graduação: o surgimento de uma impressora 3D.", in Congresso Técnico Científico da Engenharia e da Agronomia, Campina Grande, 2018, p. 22
[24] J. Ziegler and N. B. Nichols, “Optimum settings for automatic controllers,” Trans. ASME, vol. 64, pp. 759–768, 1942.
[25] K. Karunakaran, V. Pushpa, S. Akula and S. Suryakumar, "Techno-economic analysis of hybrid layered manufacturing", International Journal of Intelligent Systems Technologies and Applications, vol. 4, no. 12, p. 161, 2008.

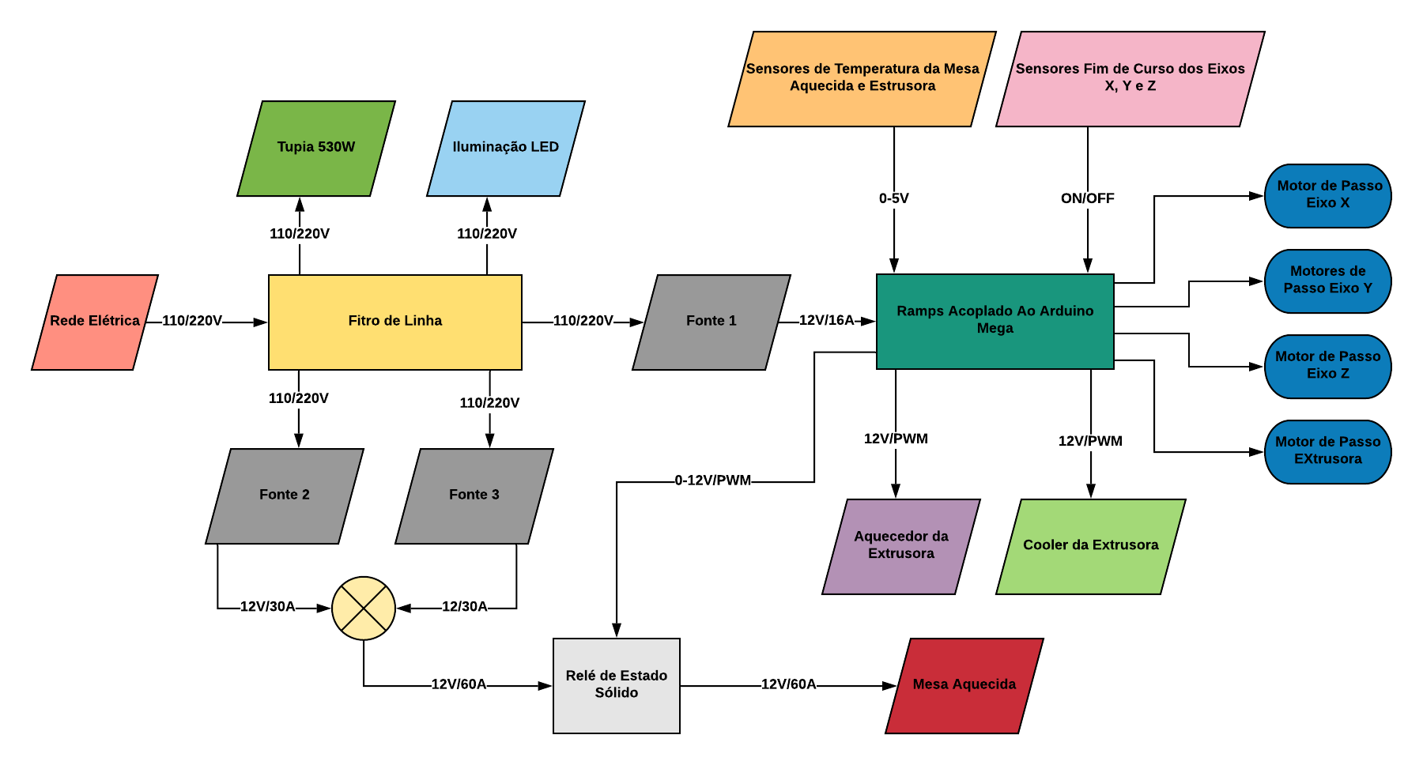
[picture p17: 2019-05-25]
Schematic/Block Diagram.png

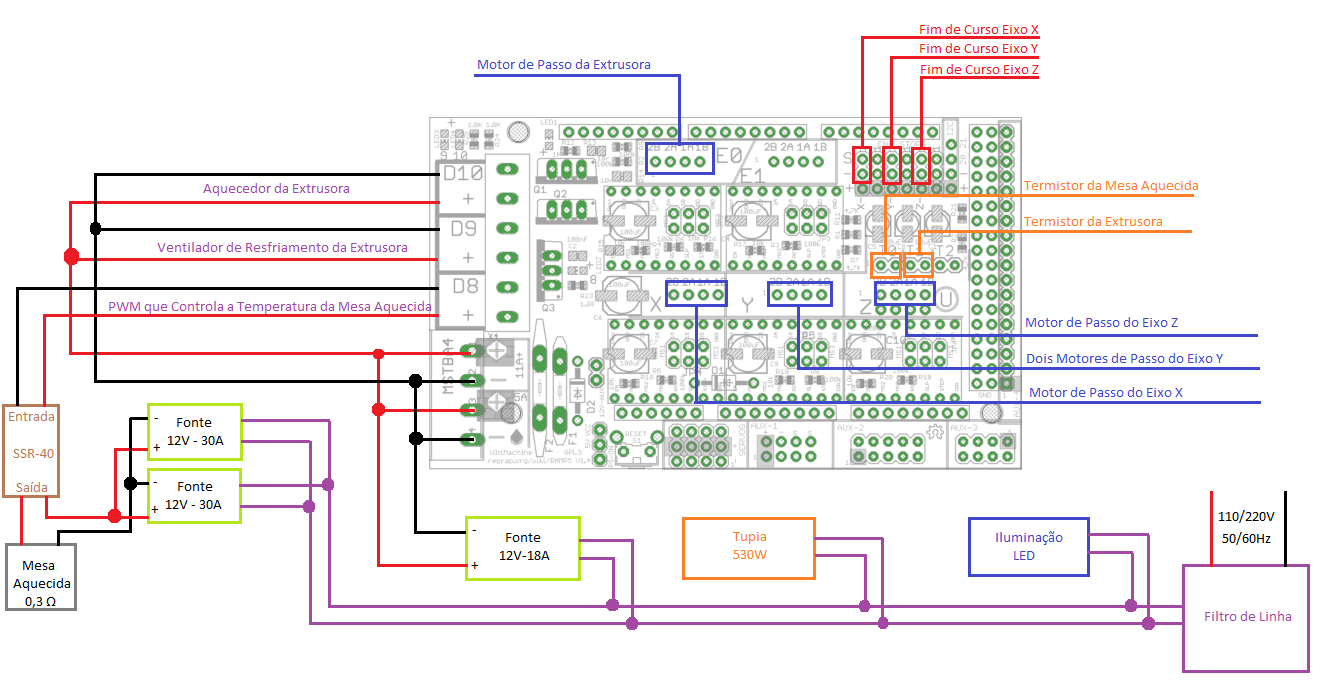
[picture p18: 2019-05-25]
Schematic/ramps1.4 v1.1.png

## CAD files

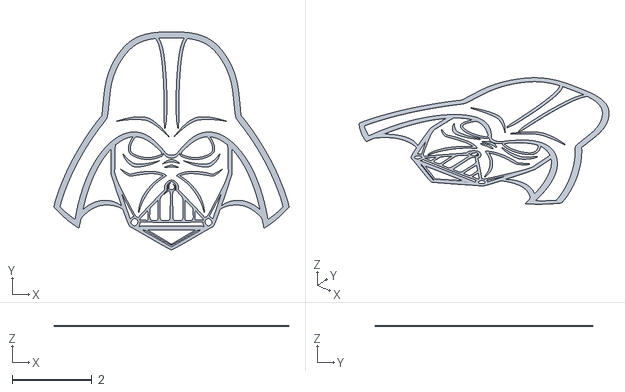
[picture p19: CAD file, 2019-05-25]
3D Models/darth vader.stl
5.89 x 5.46 x 0.02

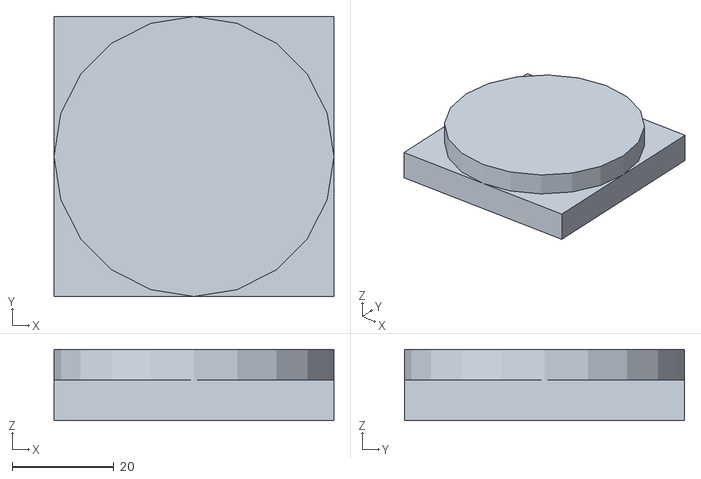
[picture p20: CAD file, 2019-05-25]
3D Models/Mancal Preenchido.stl
55.0 x 55.0 x 14.0

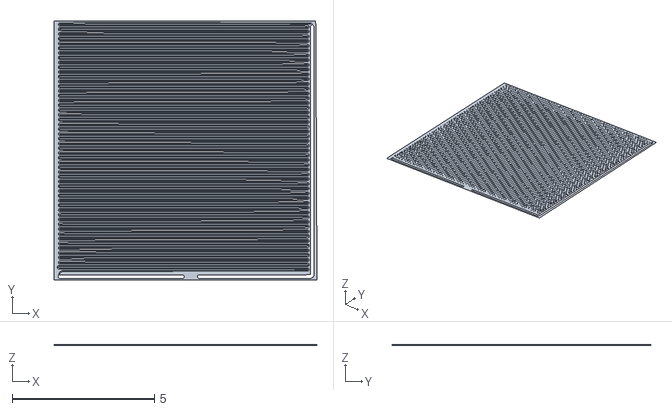
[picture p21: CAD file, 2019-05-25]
3D Models/mesa_aquecida_invertida.stl
9.26 x 9.13 x 0.02

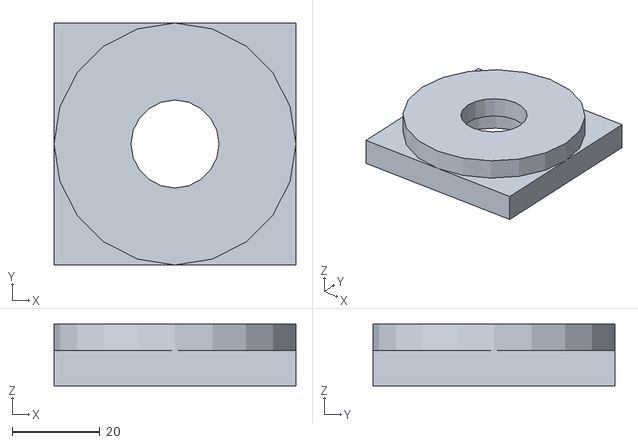
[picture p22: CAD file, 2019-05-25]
3D Models/Mancal Vazado.stl
55.0 x 55.0 x 14.0

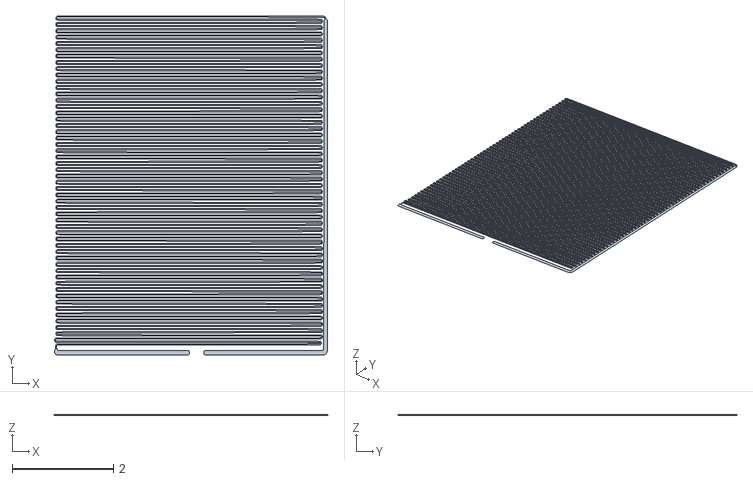
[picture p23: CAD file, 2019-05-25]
3D Models/mesa_aquecida.stl
5.40 x 6.71 x 0.0002

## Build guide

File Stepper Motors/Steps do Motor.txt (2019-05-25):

Para calcular os Steps da máquina use os parâmetros:

Fuso com 5mm por passo
Driver com 1/16 micro-passos "Definido na Ramps 1.4"
Motor 1.8 com 200 passos por revolução 

Logo 

Micropassos x 1 Revolução do motor /( Passo do Fuso)

16*200/(5) = 640 Steps/mm

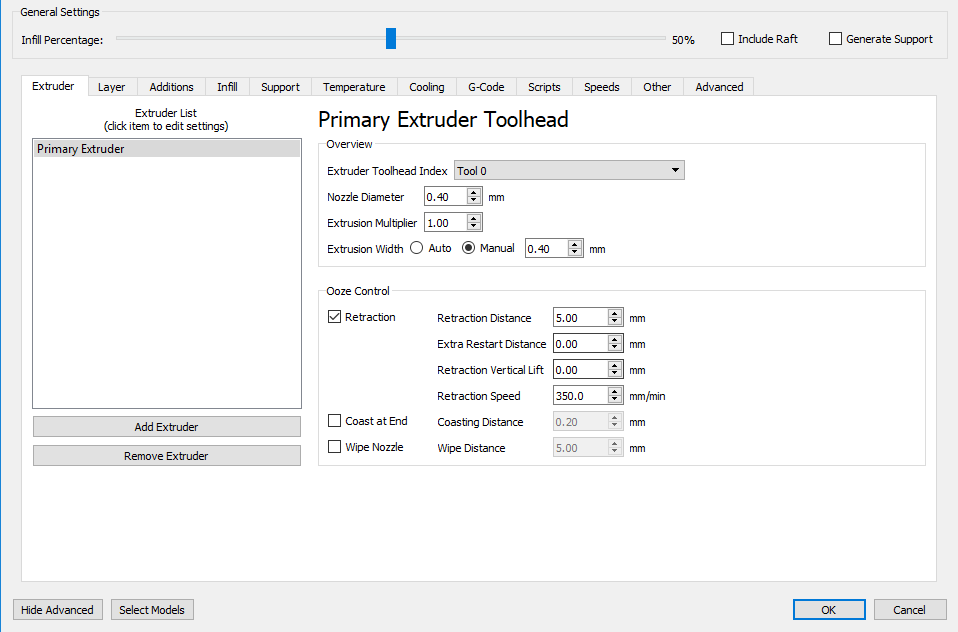
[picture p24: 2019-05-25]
3D Printer Configuration/1.PNG

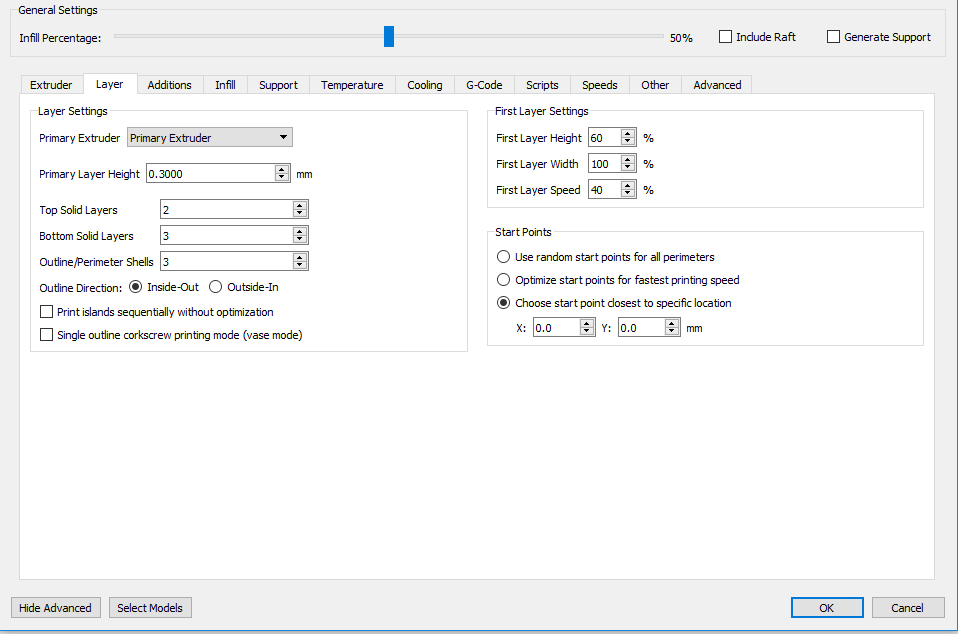
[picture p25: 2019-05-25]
3D Printer Configuration/2.PNG

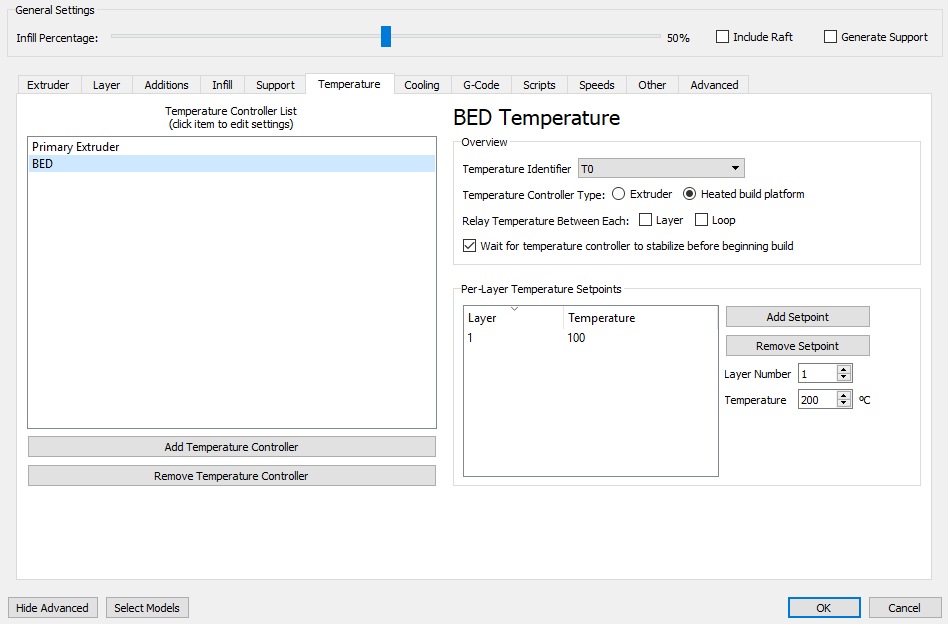
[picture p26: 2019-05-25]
3D Printer Configuration/7.PNG

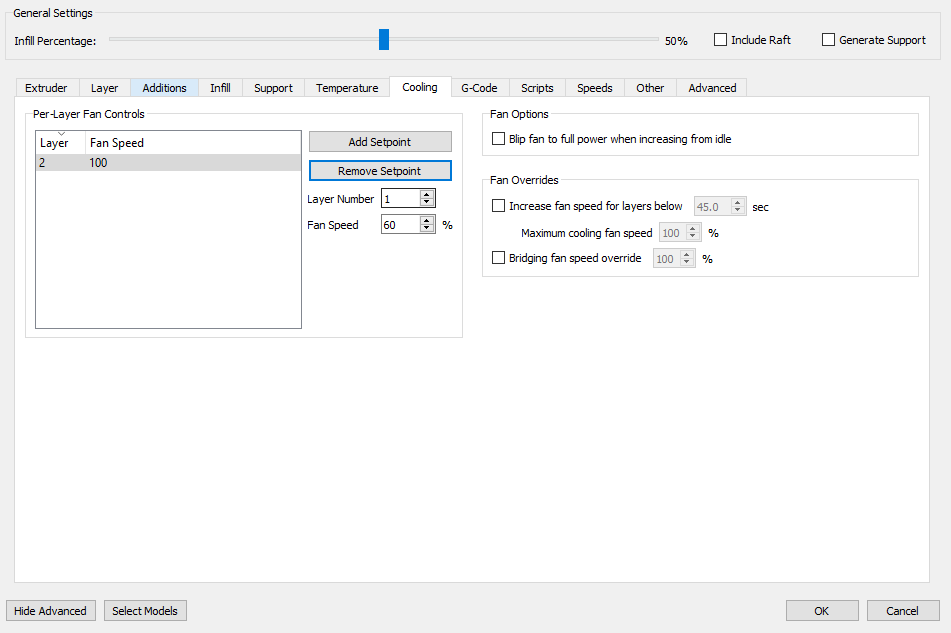
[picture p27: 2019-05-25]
3D Printer Configuration/8.PNG

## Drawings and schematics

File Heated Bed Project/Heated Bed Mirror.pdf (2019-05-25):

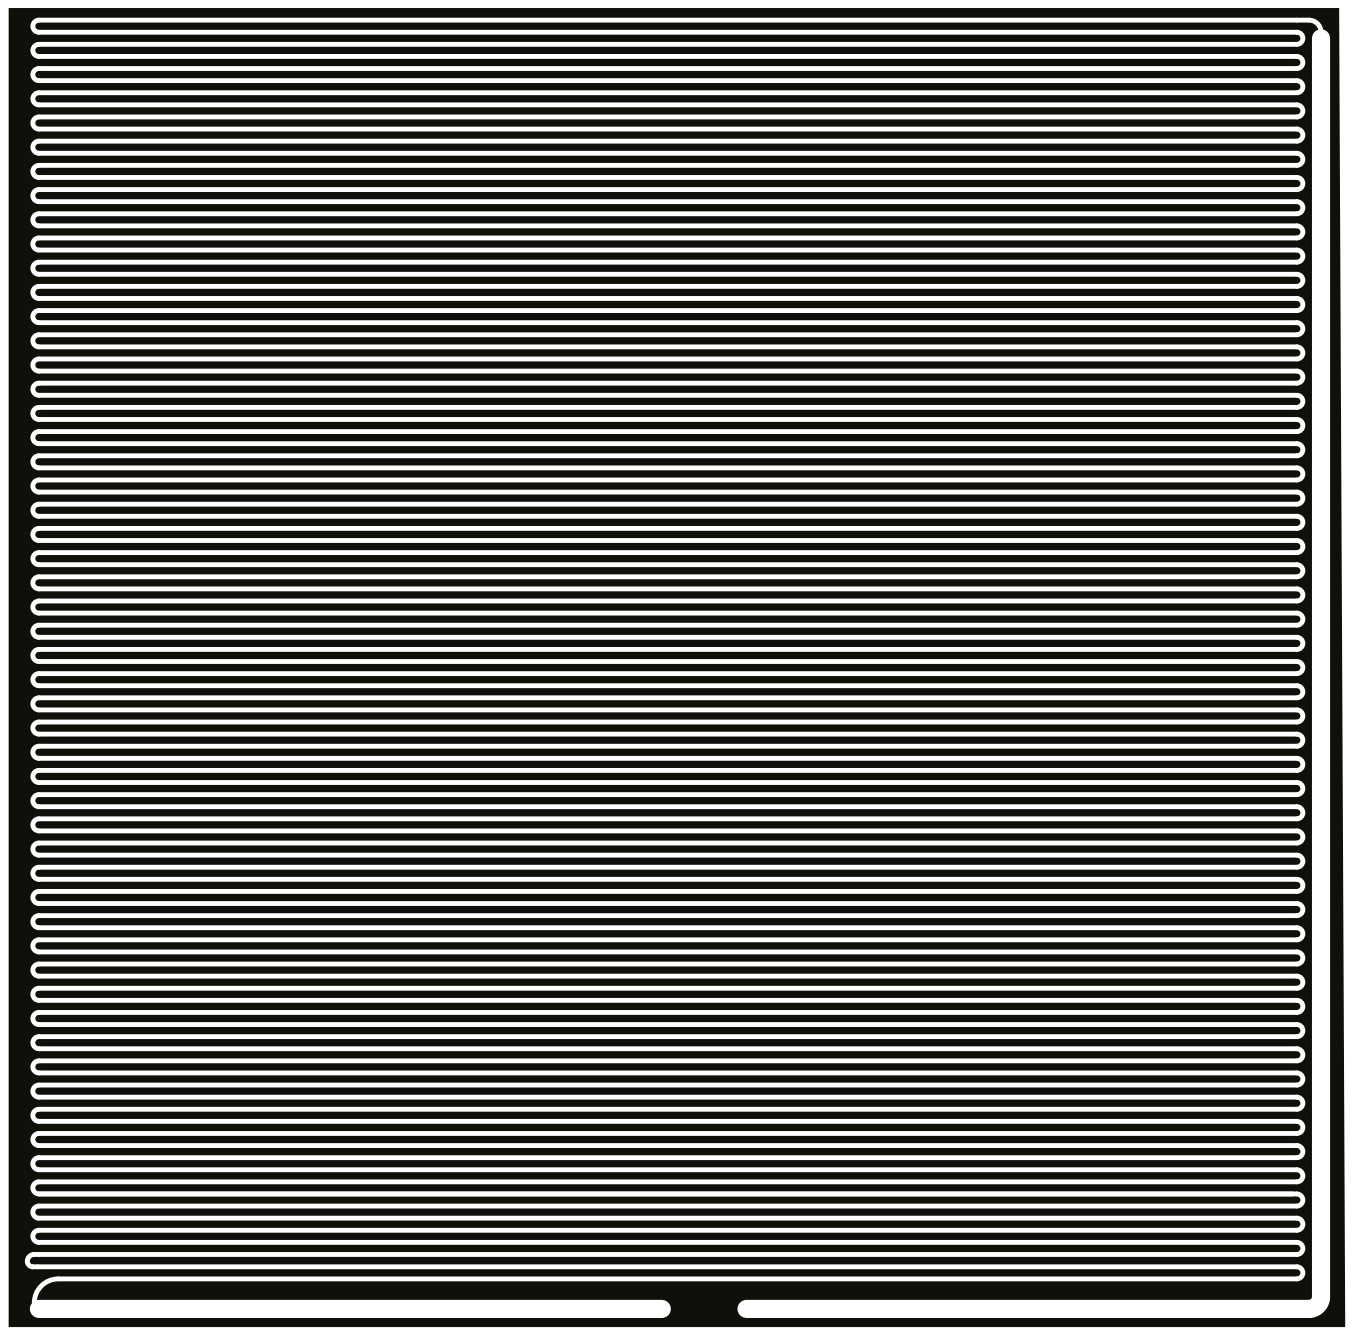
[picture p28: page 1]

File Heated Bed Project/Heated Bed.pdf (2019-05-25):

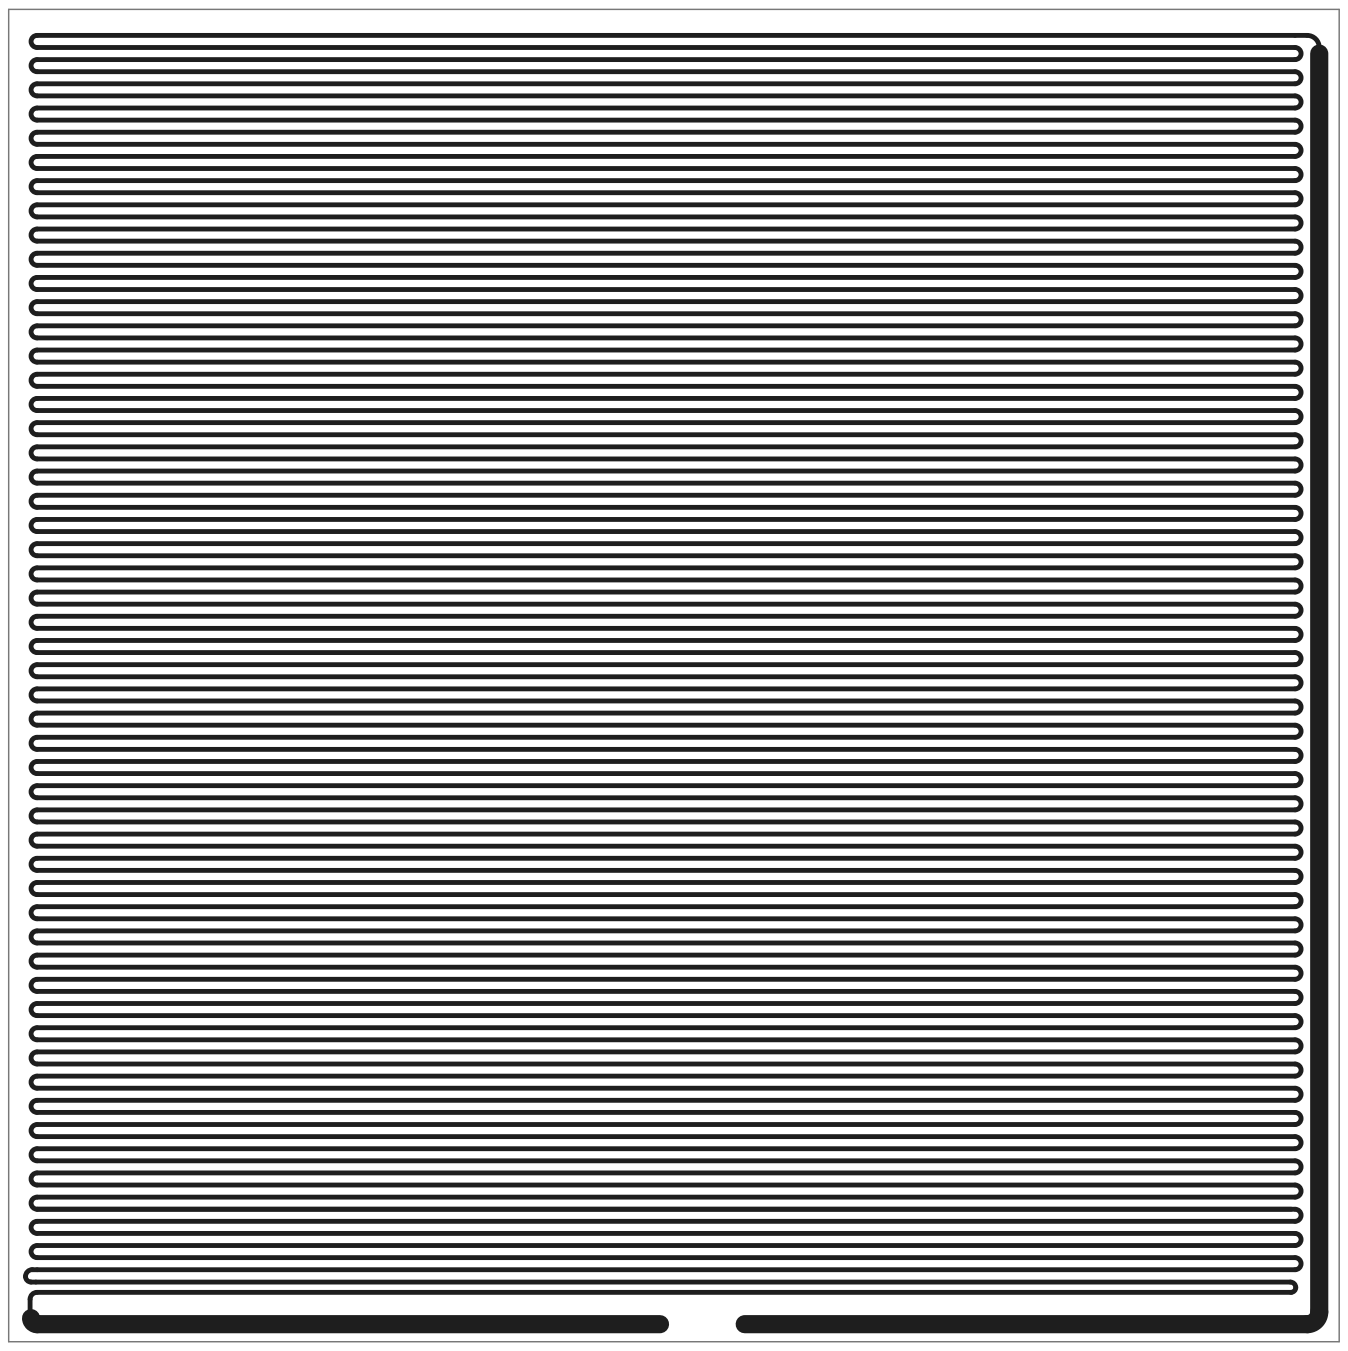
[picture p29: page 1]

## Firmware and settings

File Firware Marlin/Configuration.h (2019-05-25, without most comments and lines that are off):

#define CONFIGURATION_H
#define CONFIGURATION_H_VERSION 010107
#define STRING_CONFIG_H_AUTHOR "(none, default config)" // Who made the changes.
#define SHOW_BOOTSCREEN
#define STRING_SPLASH_LINE1 SHORT_BUILD_VERSION // will be shown during bootup in line 1
#define STRING_SPLASH_LINE2 WEBSITE_URL         // will be shown during bootup in line 2
#define SERIAL_PORT 0
#define BAUDRATE 9600
  #define MOTHERBOARD BOARD_RAMPS_14_EFB
#define CUSTOM_MACHINE_NAME "06/04/2019-v1.0"
#define EXTRUDERS 1
#define DEFAULT_NOMINAL_FILAMENT_DIA 3.0
#define POWER_SUPPLY 1
#define TEMP_SENSOR_0 1
#define TEMP_SENSOR_1 0
#define TEMP_SENSOR_2 0
#define TEMP_SENSOR_3 0
#define TEMP_SENSOR_4 0
#define TEMP_SENSOR_BED 1
#define DUMMY_THERMISTOR_998_VALUE 25
#define DUMMY_THERMISTOR_999_VALUE 100
#define MAX_REDUNDANT_TEMP_SENSOR_DIFF 10
#define TEMP_RESIDENCY_TIME 10  // (seconds)
#define TEMP_HYSTERESIS 3       // (degC) range of +/- temperatures considered "close" to the target one
#define TEMP_WINDOW     1       // (degC) Window around target to start the residency timer x degC early.
#define TEMP_BED_RESIDENCY_TIME 10  // (seconds)
#define TEMP_BED_HYSTERESIS 3       // (degC) range of +/- temperatures considered "close" to the target one
#define TEMP_BED_WINDOW     1       // (degC) Window around target to start the residency timer x degC early.
#define HEATER_0_MINTEMP 5
#define HEATER_1_MINTEMP 5
#define HEATER_2_MINTEMP 5
#define HEATER_3_MINTEMP 5
#define HEATER_4_MINTEMP 5
#define BED_MINTEMP 5
#define HEATER_0_MAXTEMP 275
#define HEATER_1_MAXTEMP 275
#define HEATER_2_MAXTEMP 275
#define HEATER_3_MAXTEMP 275
#define HEATER_4_MAXTEMP 275
#define BED_MAXTEMP 150
#define PIDTEMP
#define BANG_MAX 255     // Limits current to nozzle while in bang-bang mode; 255=full current
#define PID_MAX BANG_MAX // Limits current to nozzle while PID is active (see PID_FUNCTIONAL_RANGE below); 255=full current
#define PID_K1 0.0001      // Smoothing factor within the PID
  #define PID_FUNCTIONAL_RANGE 10 // If the temperature difference between the target temperature and the actual temperature
#define  DEFAULT_Kp 15.95
#define  DEFAULT_Ki 1.09
#define  DEFAULT_Kd 58.14
#define PIDTEMPBED
#define MAX_BED_POWER 255 // limits duty cycle to bed; 255=full current
  #define  DEFAULT_bedKp 0.0001
  #define  DEFAULT_bedKi 0.00001
  #define  DEFAULT_bedKd 1.000
#define PREVENT_LENGTHY_EXTRUDE
#define EXTRUDE_MAXLENGTH 200
#define THERMAL_PROTECTION_HOTENDS // Enable thermal protection for all extruders
#define THERMAL_PROTECTION_BED     // Enable thermal protection for the heated bed
#define USE_XMIN_PLUG
#define USE_YMIN_PLUG
#define USE_ZMIN_PLUG
#define USE_ZMAX_PLUG
#define ENDSTOPPULLUPS // Comment this out (using // at the start of the line) to disable the endstop pullup resistors
#define X_MIN_ENDSTOP_INVERTING false // set to true to invert the logic of the endstop.
#define Y_MIN_ENDSTOP_INVERTING false // set to true to invert the logic of the endstop.
#define Z_MIN_ENDSTOP_INVERTING true // set to true to invert the logic of the endstop.
#define X_MAX_ENDSTOP_INVERTING true // set to true to invert the logic of the endstop.
#define Y_MAX_ENDSTOP_INVERTING true // set to true to invert the logic of the endstop.
#define Z_MAX_ENDSTOP_INVERTING false // set to true to invert the logic of the endstop.
#define Z_MIN_PROBE_ENDSTOP_INVERTING true // set to true to invert the logic of the probe.
#define DEFAULT_AXIS_STEPS_PER_UNIT   { 640, 640, 640, 96.57}
#define DEFAULT_MAX_FEEDRATE          { 600, 600, 600, 25 }
#define DEFAULT_MAX_ACCELERATION      {600, 550, 550, 1000 }
#define DEFAULT_ACCELERATION          550    // X, Y, Z and E acceleration for printing moves
#define DEFAULT_RETRACT_ACCELERATION  550    // E acceleration for retracts
#define DEFAULT_TRAVEL_ACCELERATION   550    // X, Y, Z acceleration for travel (non printing) moves
#define DEFAULT_XJERK                 20.0
#define DEFAULT_YJERK                 20.0
#define DEFAULT_ZJERK                  0.4
#define DEFAULT_EJERK                  5.0
#define Z_MIN_PROBE_USES_Z_MIN_ENDSTOP_PIN
#define FIX_MOUNTED_PROBE
#define X_PROBE_OFFSET_FROM_EXTRUDER 0  // X offset: -left  +right  [of the nozzle]
#define Y_PROBE_OFFSET_FROM_EXTRUDER 0  // Y offset: -front +behind [the nozzle]
#define Z_PROBE_OFFSET_FROM_EXTRUDER 0   // Z offset: -below +above  [the nozzle]
#define XY_PROBE_SPEED 300
#define Z_PROBE_SPEED_FAST HOMING_FEEDRATE_Z
#define Z_PROBE_SPEED_SLOW (Z_PROBE_SPEED_FAST / 2)
#define MULTIPLE_PROBING 2
#define Z_CLEARANCE_DEPLOY_PROBE   10 // Z Clearance for Deploy/Stow
#define Z_CLEARANCE_BETWEEN_PROBES  5 // Z Clearance between probe points
#define Z_PROBE_OFFSET_RANGE_MIN 0
#define Z_PROBE_OFFSET_RANGE_MAX 20
#define X_ENABLE_ON 0
#define Y_ENABLE_ON 0
#define Z_ENABLE_ON 0
#define E_ENABLE_ON 0 // For all extruders
#define DISABLE_X false
#define DISABLE_Y false
#define DISABLE_Z false
#define DISABLE_E false // For all extruders
#define DISABLE_INACTIVE_EXTRUDER true // Keep only the active extruder enabled.
#define INVERT_X_DIR false
#define INVERT_Y_DIR true
#define INVERT_Z_DIR false
#define INVERT_E0_DIR false
#define INVERT_E1_DIR false
#define INVERT_E2_DIR false
#define INVERT_E3_DIR false
#define INVERT_E4_DIR false
#define X_HOME_DIR -1
#define Y_HOME_DIR -1
#define Z_HOME_DIR 1
#define X_BED_SIZE 285
#define Y_BED_SIZE 280
#define X_MIN_POS 0
#define Y_MIN_POS 0
#define Z_MIN_POS 0
#define X_MAX_POS X_BED_SIZE
#define Y_MAX_POS Y_BED_SIZE
#define Z_MAX_POS 20
#define MIN_SOFTWARE_ENDSTOPS
  #define MIN_SOFTWARE_ENDSTOP_X
  #define MIN_SOFTWARE_ENDSTOP_Y
  #define MIN_SOFTWARE_ENDSTOP_Z
#define MAX_SOFTWARE_ENDSTOPS
  #define MAX_SOFTWARE_ENDSTOP_X
  #define MAX_SOFTWARE_ENDSTOP_Y
  #define MAX_SOFTWARE_ENDSTOP_Z
#define AUTO_BED_LEVELING_LINEAR
#define DEBUG_LEVELING_FEATURE
  #define GRID_MAX_POINTS_X 4
  #define GRID_MAX_POINTS_Y GRID_MAX_POINTS_X
  #define LEFT_PROBE_BED_POSITION 20
  #define RIGHT_PROBE_BED_POSITION 280
  #define FRONT_PROBE_BED_POSITION 20
  #define BACK_PROBE_BED_POSITION 280
  #define MIN_PROBE_EDGE 10
#define HOMING_FEEDRATE_XY (10*65)
#define HOMING_FEEDRATE_Z  (10*65)
#define EEPROM_SETTINGS // Enable for M500 and M501 commands
#define EEPROM_CHITCHAT   // Give feedback on EEPROM commands. Disable to save PROGMEM.
#define HOST_KEEPALIVE_FEATURE        // Disable this if your host doesn't like keepalive messages
#define DEFAULT_KEEPALIVE_INTERVAL 2  // Number of seconds between "busy" messages. Set with M113.
#define BUSY_WHILE_HEATING            // Some hosts require "busy" messages even during heating
#define PREHEAT_1_TEMP_HOTEND 180
#define PREHEAT_1_TEMP_BED     70
#define PREHEAT_1_FAN_SPEED     0 // Value from 0 to 255
#define PREHEAT_2_TEMP_HOTEND 240
#define PREHEAT_2_TEMP_BED    110
#define PREHEAT_2_FAN_SPEED     0 // Value from 0 to 255
#define PRINTJOB_TIMER_AUTOSTART
#define LCD_LANGUAGE en
#define DISPLAY_CHARSET_HD44780 JAPANESE
#define SOFT_PWM_SCALE 0
#define SERVO_DELAY { 300 }

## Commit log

2019-05-25 Firmware Marlin
    First Commit
    [Configuration.h, Configuration_adv.h]
2019-05-25 Others
    Initial Commit
    [Mancal Preenchido.stl, Mancal Vazado.stl, darth vader.stl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]
2019-05-25 Create Diagrama de Blocos.png

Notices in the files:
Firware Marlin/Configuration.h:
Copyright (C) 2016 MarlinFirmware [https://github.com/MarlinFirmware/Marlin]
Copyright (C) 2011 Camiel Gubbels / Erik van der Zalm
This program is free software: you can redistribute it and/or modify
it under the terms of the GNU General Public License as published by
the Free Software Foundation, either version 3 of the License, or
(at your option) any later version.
